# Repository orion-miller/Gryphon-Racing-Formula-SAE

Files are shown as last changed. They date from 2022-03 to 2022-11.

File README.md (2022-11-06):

# About
The chance to be a member of the Gryphon Racing Formula SAE team was the highlight of my time at the University of Guelph. The role helped me to appreciate the complexity of real-world systems, the necessity to make data driven decisions while remembering the limitations of my knowledge and methods, and the need for validation of results and continual reassessment. The race team was a way to gain practical experience across many stages of the engineering process, such as systems analysis, mechanical design, CAD, structural analysis and FEA, and manufacturing.

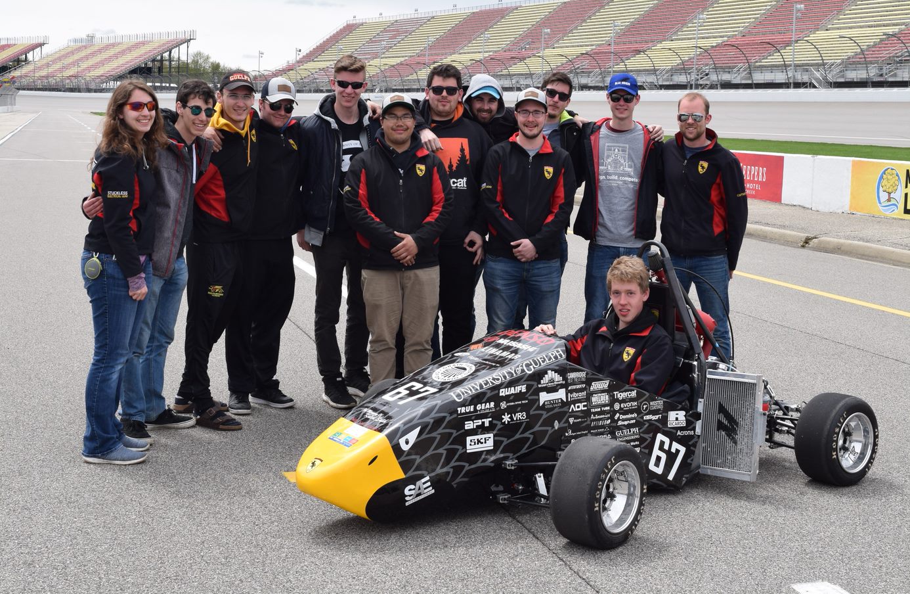
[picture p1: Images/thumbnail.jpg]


---

> ### 2018-2019: Suspension Lead
> • Managed a team of 7 people carrying out the design and manufacturing of suspension and steering components  
• Responsible for performing vehicle dynamics analysis to set systems-level design goals for an open wheeled race car   
• Designed all-new suspension and steering setups for an updated 10" wheel package  
• Manufactured numerous parts including bellcranks, suspension links, anti-roll bars, steering column, etc.  
• Received highest Suspension Design score at competition since team inception in 2002, and was one of the team's 4 competition drivers  
• Developed a MATLAB based program for visualizing tire test data and fitting Semi-Empirical Pacejka tire models, using data generated by the FSAE Tire Testing Consortium  
• Completed two group design projects for course credit, developing a carbon fibre rim design and shock dynomometer

> ### 2017-2018: Suspension Member
> • Design and manufacturing of custom steering rack and steering column assembly  
• Machining of various parts using manual mill, manual lathe, CNC mill  
• Attendance of team events for sponsorship and promotion  

> ### 2016-2017: Chassis Member
> • Helped with building of a steel space frame chassis & general fabrication for frame components   
• Design of pedal box assembly  

---
## Design & Manufacturing Work - Examples
---

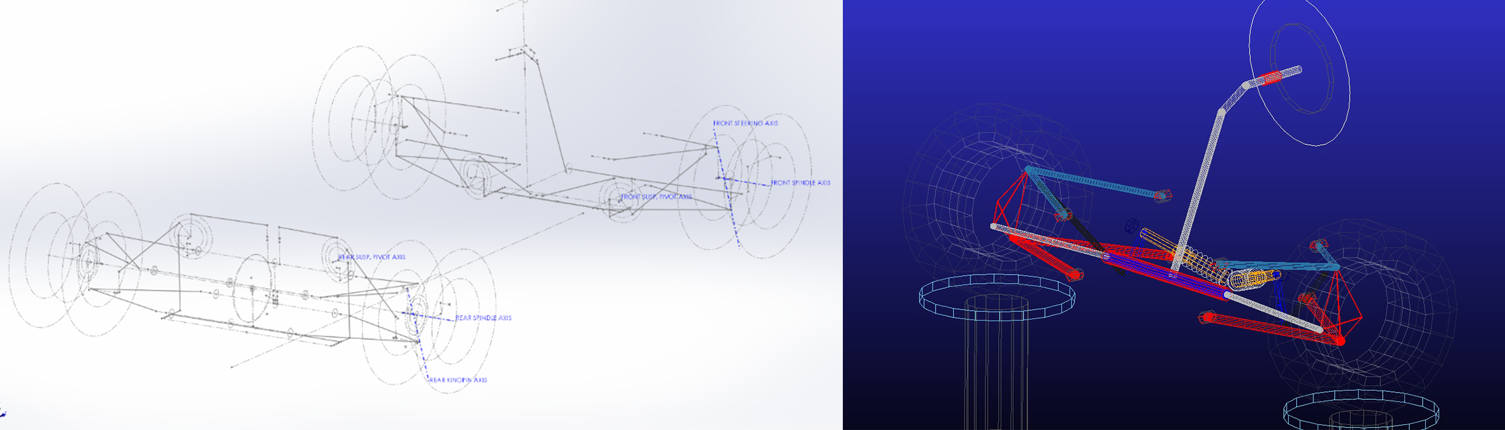
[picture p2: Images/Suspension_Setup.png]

*2019 Suspension Setup*

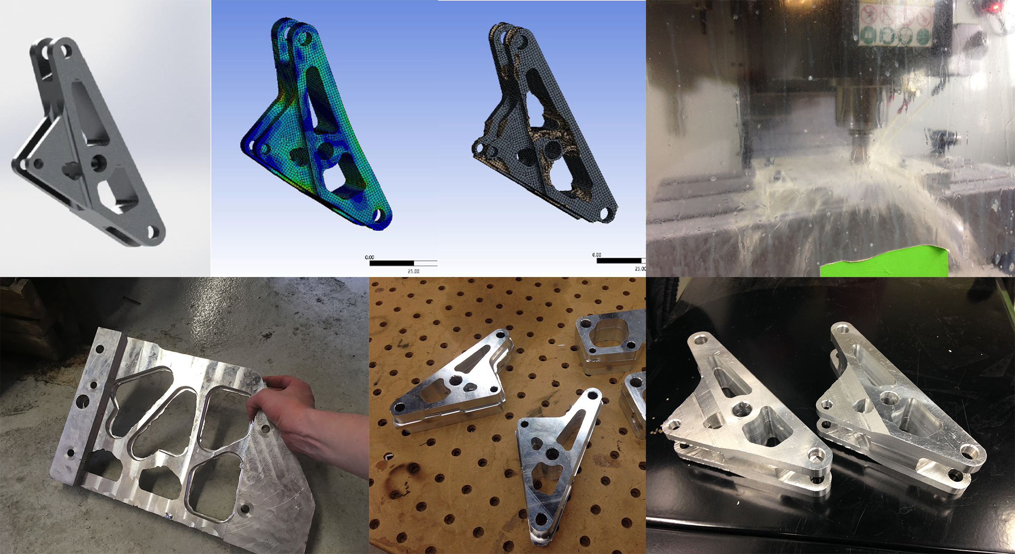
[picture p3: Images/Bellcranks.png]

*Bellcranks*

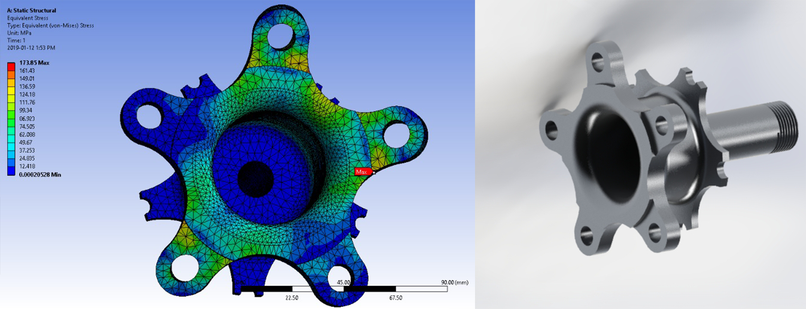
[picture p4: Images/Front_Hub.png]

*Front Hubs*

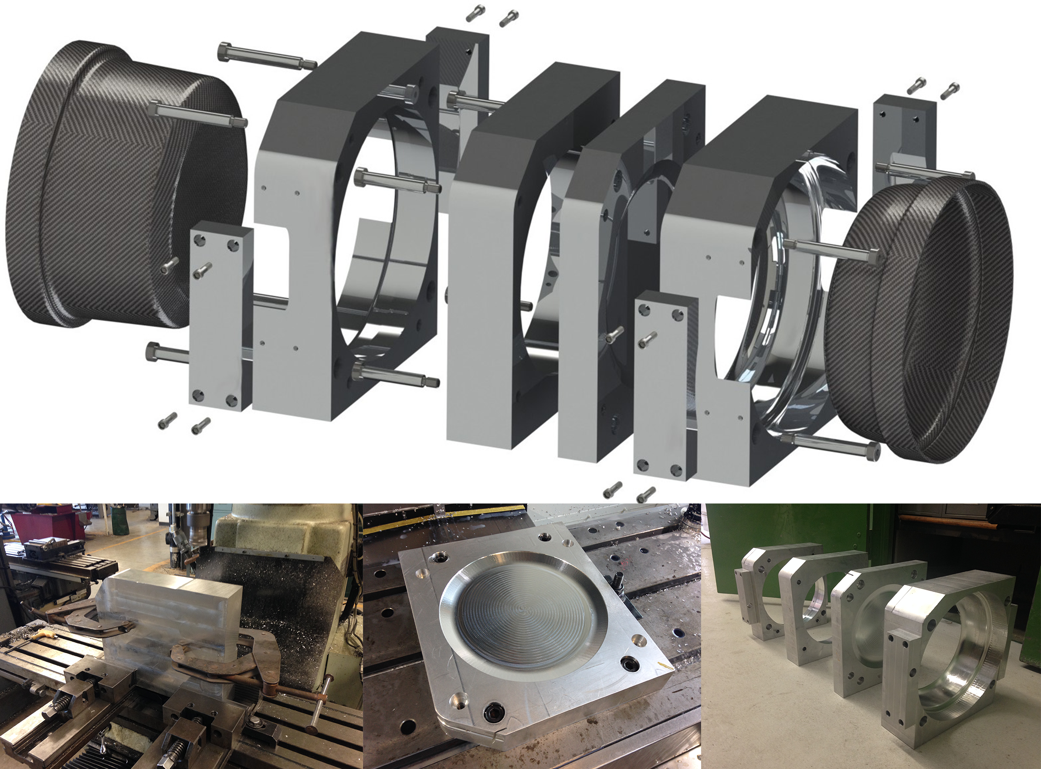
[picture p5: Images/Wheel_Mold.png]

*Carbon Fiber Rim Mold*

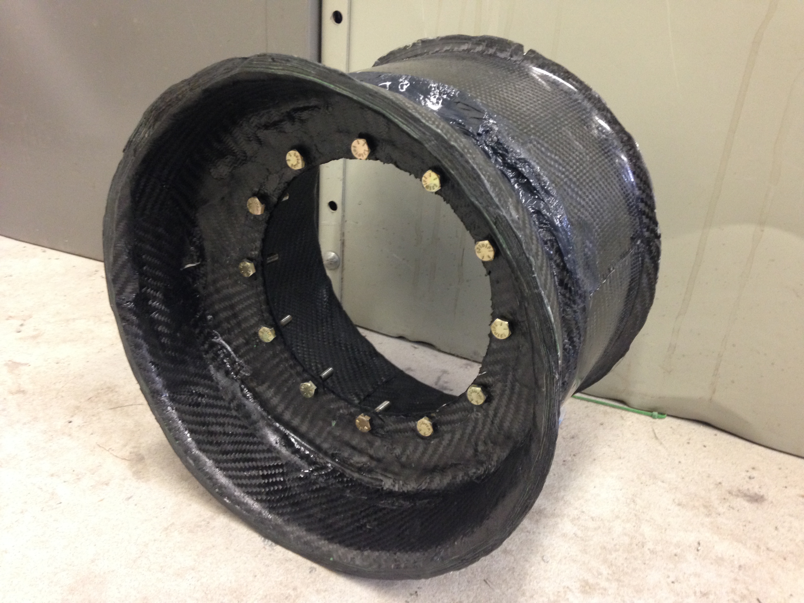
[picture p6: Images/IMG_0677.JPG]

*Carbon Fiber Rim*

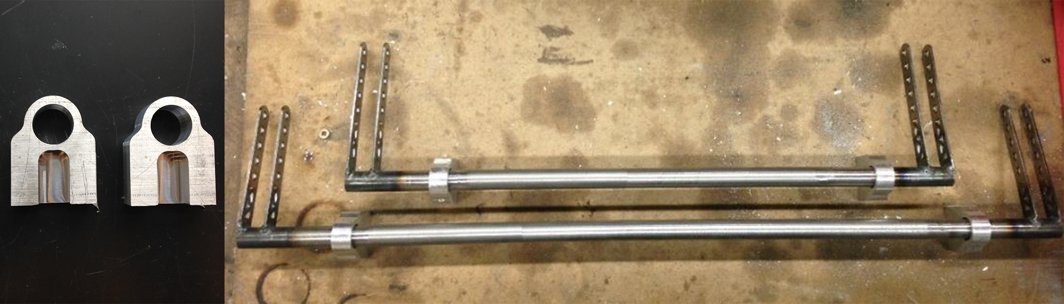
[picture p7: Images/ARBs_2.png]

*Anti-Roll bars*

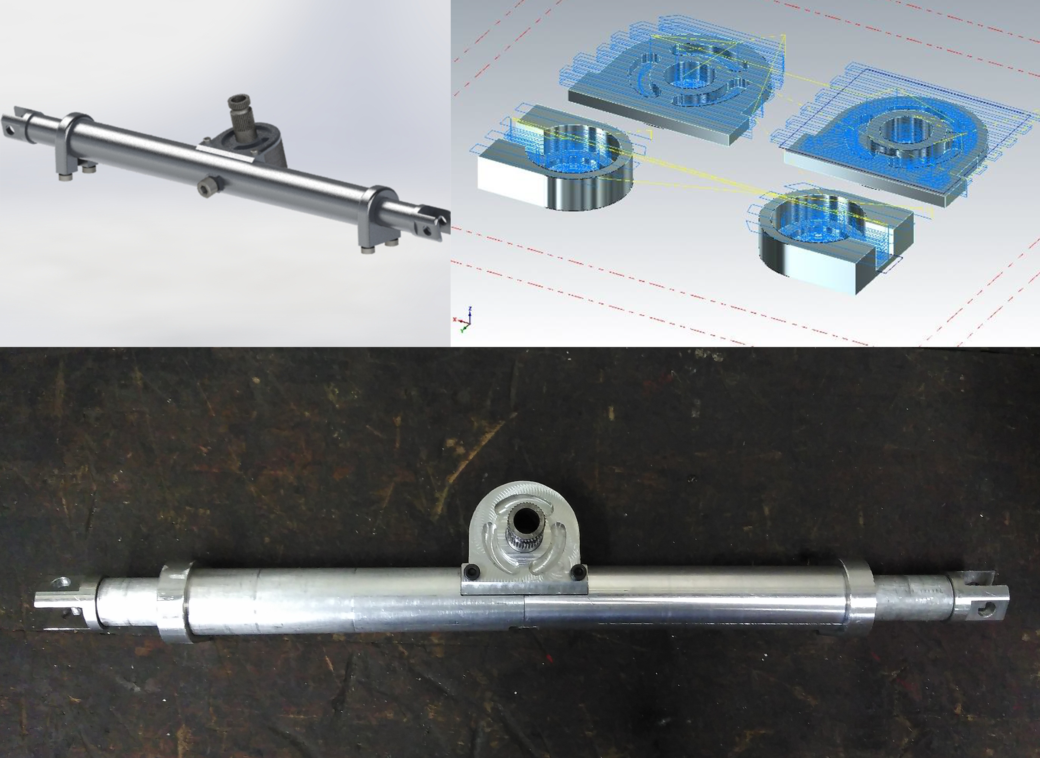
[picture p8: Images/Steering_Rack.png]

*Custom Steering Rack*

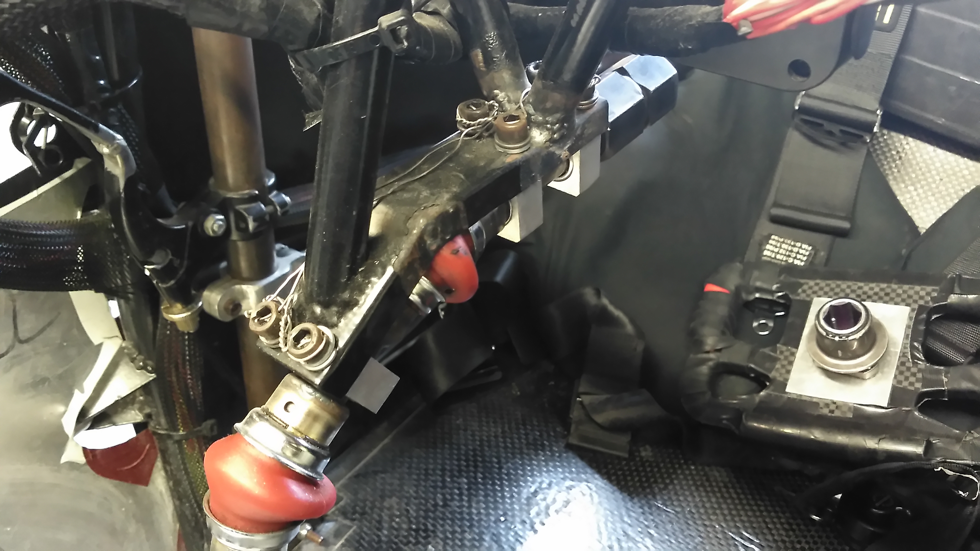
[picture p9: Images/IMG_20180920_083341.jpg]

*Steering Column*

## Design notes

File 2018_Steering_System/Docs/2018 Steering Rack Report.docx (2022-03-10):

Orion Miller 2018 Custom Steering Rack Report April 21st, 2018.

Background

In the teams most recent car (GRC-17), a Kaz Technologies steering rack is used in a bottom mount, rear steer configuration. This rack is reliable and functions well, however when scrutinizing the overall weight of the system, there appear to be opportunities for improvement.

Firstly, the location of the mounts on the rack created the need to add two more frame members through the middle of the cockpit floor. The weight of these tubes is estimated to be 441 grams (0.83 lbs). If a slightly longer rack were used, it would be possible to avoid this by mounting on to the existing outside frame members.

Secondly, a different material could be chosen for the rack gear. Using aluminum over steel would reduce weight significantly for such a large component. The density of steel is 7700 kg/m³, whereas aluminum is only 2700 kg/m³. The reason aluminum is less commonly used is because aluminum gears are prone to galling. However, the life cycle of an FSAE car is quite short, and the weight reduction benefits are large enough to justify the inconvenience of possibly having to replace the rack gear on a yearly basis.

Design Goals

Because of the lack of available steering racks that are designed to mount on the outside of the frame, are lighter than the Kaz rack, and are affordable, the development of a custom rack is the best option. The requirements for this design are as follows:

Constraints

- This rack should have a similar speed ratio (4.8 in/rev) and overall travel (3.25”) to the previous system, because the team was satisfied with its performance.
- The journal bearings should be mounted on the outside of the system to minimize the lengths of the bending moments for the longer rack gear.
- The housing of the system needs to effectively keep the grease in, and any dust or dirt out.
- The system needs to be built to withstand estimated maximum steering forces of 2000 N.
- Because reliability is critical for a steering system, all components must be designed for a factor of safety of 1.5 or greater.

Criteria

Development

Checking the geometry of the frame in CAD, the outside frame members are around 320 mm apart in the section where the system would be mounted. If brackets are attached on the immediate inside of these tubes, a distance between mounts of 300-305 mm should be suitable.

A pinion gear with a speed ratio of 4.8 in/rev from a previous year’s steering rack was selected.

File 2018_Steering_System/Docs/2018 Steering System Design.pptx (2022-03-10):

## 2018 Steering System Design

## Steering Rack

## Last Year’s Setup

- Functioned well
- Ackermann and speed ratio could be increased
- Heavy

## Design Goals/Constraints

- Rack must mount on outside of the frame
- Make lighter than previous
- Keep handling parameters the same
- We have to be able to make it
- Keep cost down

## What decisions were made?

- Aluminum rack
- Same gearing
- Carbon Fiber in Housing
- Slightly less overall travel (less rack teeth)
- Place bushings on outside
- Lash adjustment

## Steering Column

## Last Year’s Setup

- Compliance
- Heavy

## Design Goals/Constraints

- Simplify/reduce housing material
- Reduce compliance
- Look into shortening attaching frame members
- Joints must run under acceptable angles

## What decisions were made?

- Two shaft setup with double u-joint. Allows for Ackermann we want, simpler to constrain well
- Use same kind of U-joints, shafts, quick release
- Change from ball bearings to needle roller bearings
- Make replacement quick release hex from aluminum

## Weight Savings

- Steering Rack

- Steering Column

- Steering Rack: 1404g → 746g = 658g
- Support Material: 441g → 46g = 395g
TOTAL = 1448 grams = 3.19 lbs

- Steering Column: 617g → 498g = 119g
- Steering Housing: 296g → 111g = 185g
- Support Material: Save 91 grams

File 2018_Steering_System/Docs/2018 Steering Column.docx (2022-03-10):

2018 Steering Column

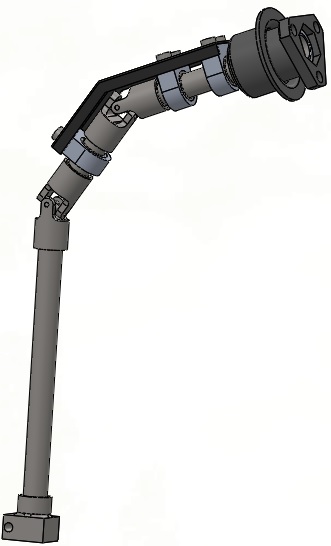
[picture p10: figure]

Specifications:

Total Weight = 1.59 lbs = 720.0 grams

Material: 1018 Steel, Aluminum

Joint Angles: 34 degrees (In Phase)

Wall Thickness = 0.035” (Minimum)

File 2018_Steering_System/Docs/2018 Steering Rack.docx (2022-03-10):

2018 Steering Rack

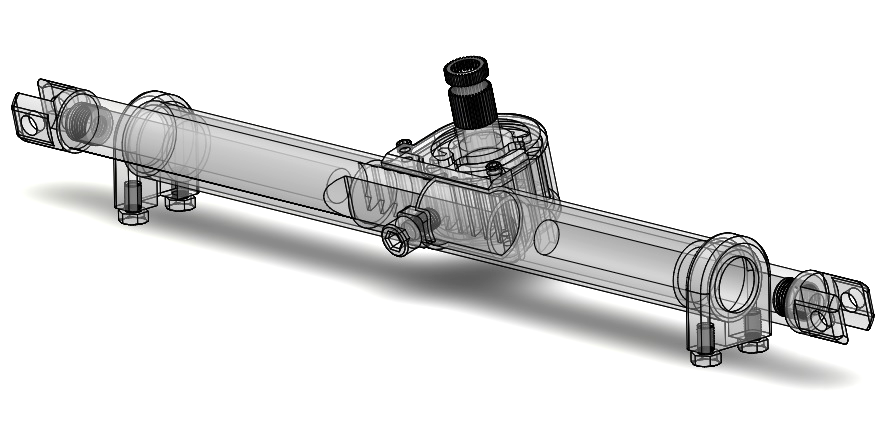
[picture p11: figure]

Specifications:

Total Weight = 1.64 lbs = 743.5 grams

Material: 6061 Aluminum, High Carbon Steel, Carbon Fiber

Length (Pickup to Pickup) = 15.96 in = 404.5 mm

Total Travel = 2.7 in = 68 mm

Speed Ratio = 4.81 in/rev

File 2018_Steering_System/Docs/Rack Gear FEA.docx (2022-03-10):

# Steering Rack FEA 04/25/2019

# Assumptions

- Resultant force of 2000N applied at a 15 degree angle
- Support reaction occurs on the face of a single tooth
- Rack surface is a frictionless slider

# Material Properties

Model Reference | Properties

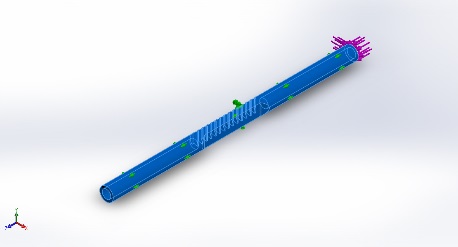
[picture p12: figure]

| Name: 6061-T6 (SS) Model type: Linear Elastic Isotropic Default failure criterion: Unknown Yield strength: 2.75e+008 N/m^2 Tensile strength: 3.1e+008 N/m^2 Elastic modulus: 6.9e+010 N/m^2 Poisson's ratio: 0.33 Mass density: 2700 kg/m^3 Shear modulus: 2.6e+010 N/m^2 Thermal expansion coefficient: 2.4e-005 /Kelvin

Mesh Details

- Mesh Type: Automatic
- Number of Cells: 13875
- Refinement: No
- Topology Criteria: NA
- Topology Percentage: NA

# Loads and Fixtures

Fixture Name | Fixture Image | Fixture Details

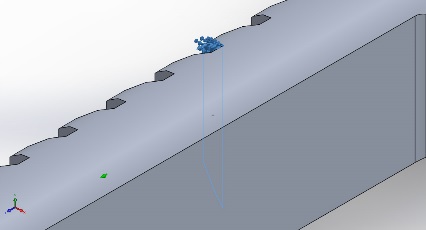
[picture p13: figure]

Fixed-5 | | Entities: 1 face(s) Type: Fixed Geometry

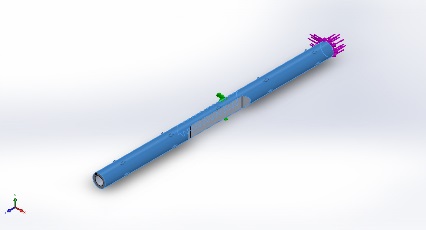
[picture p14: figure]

Roller/Slider-4 | | Entities: 1 face(s) Type: Roller/Slider

Load Name | Load Image | Load Details

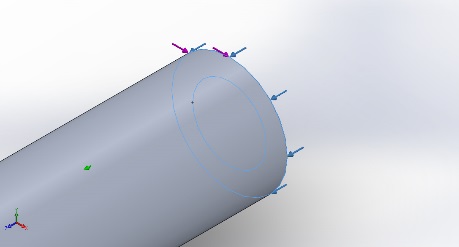
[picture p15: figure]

Force-3 | | Entities: 1 face(s) Type: Apply normal force Value: 1930 N

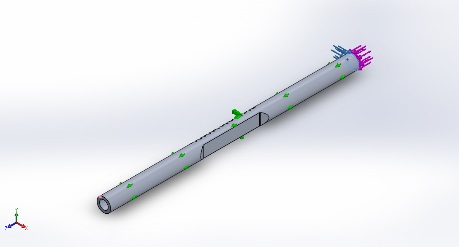
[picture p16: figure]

Force-4 | | Entities: 1 face(s) Type: Apply force Values: 520 N

# Study Results

Name | Type | Max
Stress | VON: von Mises Stress | 1.648e+007N/m^2

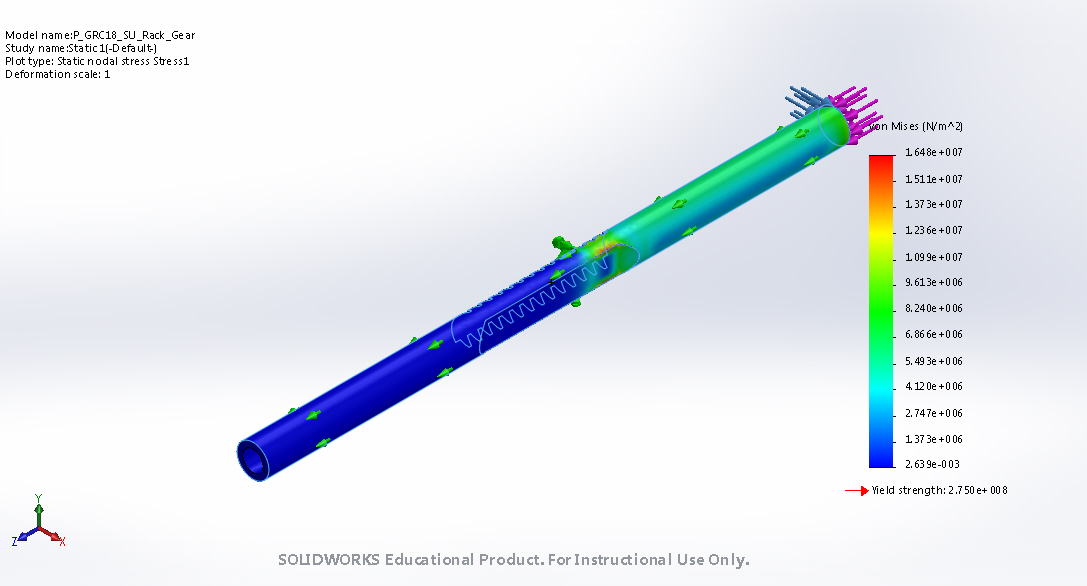
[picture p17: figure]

Name | Type | Max
Displacement | URES: Resultant Displacement | 2.464e-002mm

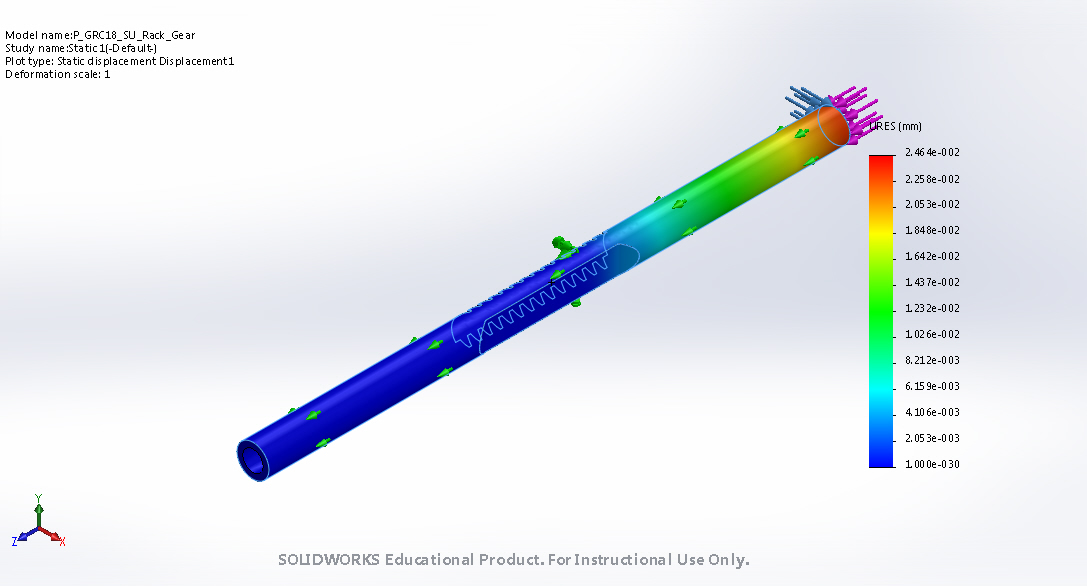
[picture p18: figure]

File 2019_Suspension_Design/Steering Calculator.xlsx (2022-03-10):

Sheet: Steering Radius
VARIABLE |  | UNITS | VARIABLE |  | UNITS
Wheelbase | 1.55 | m | CG X-Location | 0.8 | m
Rear Track | 1.196 | m | CG Y-Location | 0 | m
Front Track | 1.231 | m | Rear Inside Fx | 1000 | N
Rear Inside Slip Angle | 3.1 | deg. | Rear Inside Fy | 1200 | N
Rear Outside Slip Angle | 4.4 | deg. | Rear Inside Mz | 50 | N.m
Front Inside Slip Angle | 7.2 | deg. | Rear Outside Fx | 1500 | N
Front Outside Slip Angle | 8.8 | deg. | Rear Outside Fy | 2000 | N
Turn Radius | 4 | m | Rear Outside Mz | 50 | N.m
REQUIRED GEOMETRY |  |  | Front Inside Fx | 1000 | N
Inside Steering Angle | 24.62 | deg. | Front Inside Fy | 1400 | N
Outside Steering Angle | 22.23 | deg. | Front Inside Mz | 50 | N.m
Ackermann Angle | 2.38 | deg. | Front Outside Fx | 1300 | N
 |  |  | Front Outside Fy | 1700 | N
 |  |  | Front Outside Mz | 50 | N.m
Sources of Inaccuracy |  |  | Aerodynamic Mz | 80 | N.m
What slip angles should be used? |  |  | Yaw Moment | 8075.65 | N.m
**Trig stuff - don't worry about what these are** |  |  | **Counterclockwise Rotation is Positive**
Rear Angle | 3.75 | deg. | **CG X-Location is distance from back of car to CG**
Rear y dist to center | 4.598 | m | **Positive CG Y is towards the outside of the car**
Rear x dist | 0.3005097892 | m | M1 | 598
Front inside x dist | 1.249490211 | m | M2 | 960
front inside y dist | 3.9825 | m | M3 | 897
front outside x dist | 1.249490211 | m | M4 | 1600
front outside y dist | 5.231 | m | M5 | 615.5
front inside w/o slip | 17.41899825 | deg. | M6 | 1050
front outside w/o slip | 13.43409791 | deg. | M7 | 800.15
 |  |  | M8 | 1275

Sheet: S.S. Steering Effort
VARIABLE | OUTSIDE TIRE | INSIDE TIRE | UNITS
Mz | 100 | 80 | N.m
Pneumatic Trail | 0.03 | 0.03 | m
Mechanical Trail | 0.04 | 0.04 | m
Steering Pickup Length | 0.055 |  | m
Steer Angle (δ) | 20 | 25 | deg.
Tie-Rod Length | 0.35 |  | m
Tie-Rod Angle (θ) | 18 | 14 | deg.
Pinion Gear Pitch Radius | 0.018 |  | m
Steering Wheel Width | 0.12 |  | m
SYSTEM FORCES
Resultant Lateral Force on Tire | 1428.57 | 1142.86 | N
Force on Upright Pickup | 1818.18 | 1454.55 | N
Tie-Rod Force | 1819.29 | 1871.65 | N
Axial Force at Rack Clevis | 1730.25 | 1816.05 | N
Transverse Force at Rack Clevis | 562.19 | 452.79 | N
Axial Force Reacted By Pinion | 3546.30 |  | N
Force at Wheel | 531.95 |  | N
Sources of Inaccuracy
Where do Mz's and pneumatic trail come from?

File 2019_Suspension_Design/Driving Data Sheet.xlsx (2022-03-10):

GRYPHON RACING TEST DAY SHEET
DATE: | AIR TEMP: |  |  | WEATHER:
TIME: | ROAD TEMP: |  |  | LOCATION:
TEST PLAN:
 | FR | FL | RR | RL | NOTES
SHOCK PRELOAD |  |  |  |  | mm, measure exposed threads
CORNER WEIGHT |  |  |  |  | lbs
WEIGHT DISTRIBUTION |  |  |  |  | %
BRAKE BALANCE |  |  |  |  | %
CAMBER |  |  |  |  | colours of shims
TOE |  |  |  |  | deg
SHOCK SPRING RATE |  |  |  |  | lbs/in
SHOCK LSC |  |  |  |  | clicks from closed
SHOCK HSC |  |  |  |  | clicks from closed
SHOCK LSR |  |  |  |  | clicks from closed
SHOCK HSR |  |  |  |  | clicks from closed
ARB POSITION (1-5) |  |  |  |  | 1-5, 5 tightest
TIRE TEMP INSIDE - START |  |  |  |  | C
TIRE TEMP CENTER - START |  |  |  |  | C
TIRE TEMP OUTSIDE - START |  |  |  |  | C
TIRE PRESSURE - START |  |  |  |  | psi
TIRE TEMP INSIDE - END |  |  |  |  | C
TIRE TEMP CENTER - END |  |  |  |  | C
TIRE TEMP OUTSIDE - END |  |  |  |  | C
TIRE PRESSURE - END |  |  |  |  | psi
GAS LEVEL |  | ENGINE TUNE
GAS BATCH
OIL LEVEL |  | CV GREASE
OIL BATCH |  | FUEL FILTER
COOLANT LEVEL |  | AIR FILTER
DRIVER FEEDBACK (AS SPECIFIC AS POSSIBLE) AND CHANGE NOTES:

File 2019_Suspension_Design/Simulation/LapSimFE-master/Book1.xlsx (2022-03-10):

Classes | Notes | Functions | Notes
Motor | Should be complete except for commenting. Optimization is complete. Needs torque and efficiency data.
Battery | Not Started
Driveline | Not Started
Suspension | Not Started
CarTire | Currently defined by a simple GG curve Current state is fully documented
Brakes | Not Started
Car | Old version still available, can possibly rip a few methods out of there
Track | Completed
Track Section | Needs to add throttle/brake curve property Current state is fully documented

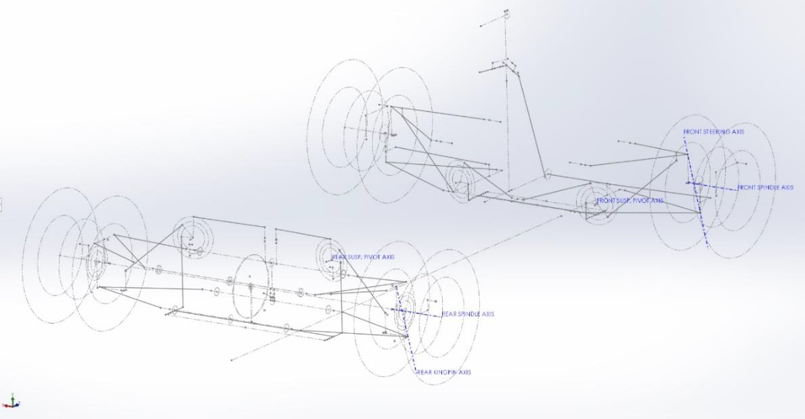
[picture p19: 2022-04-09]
Images/Design_Sketches.png

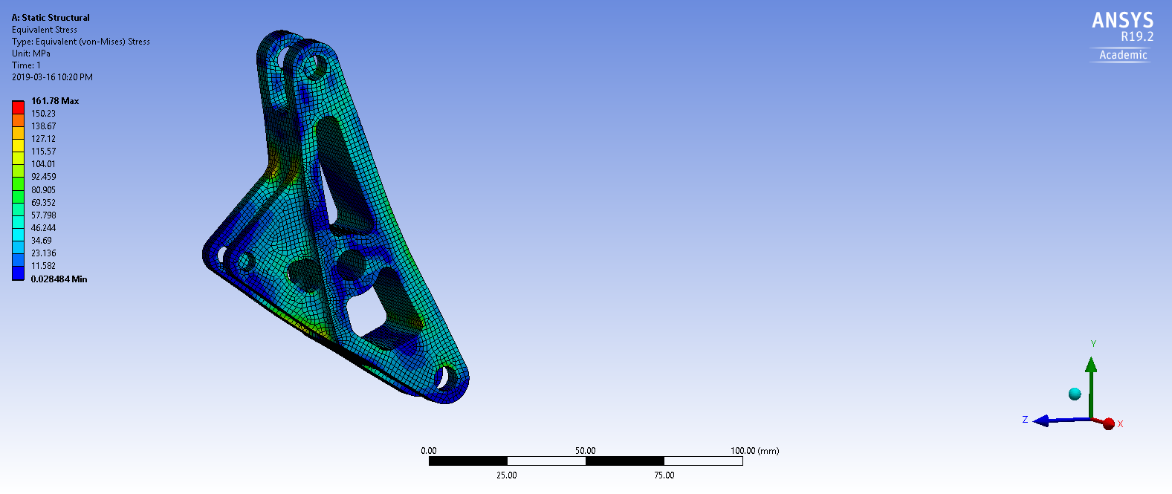
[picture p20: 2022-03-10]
2019_Suspension_Design/Screenshots & Pictures/Renders/Untitled.png

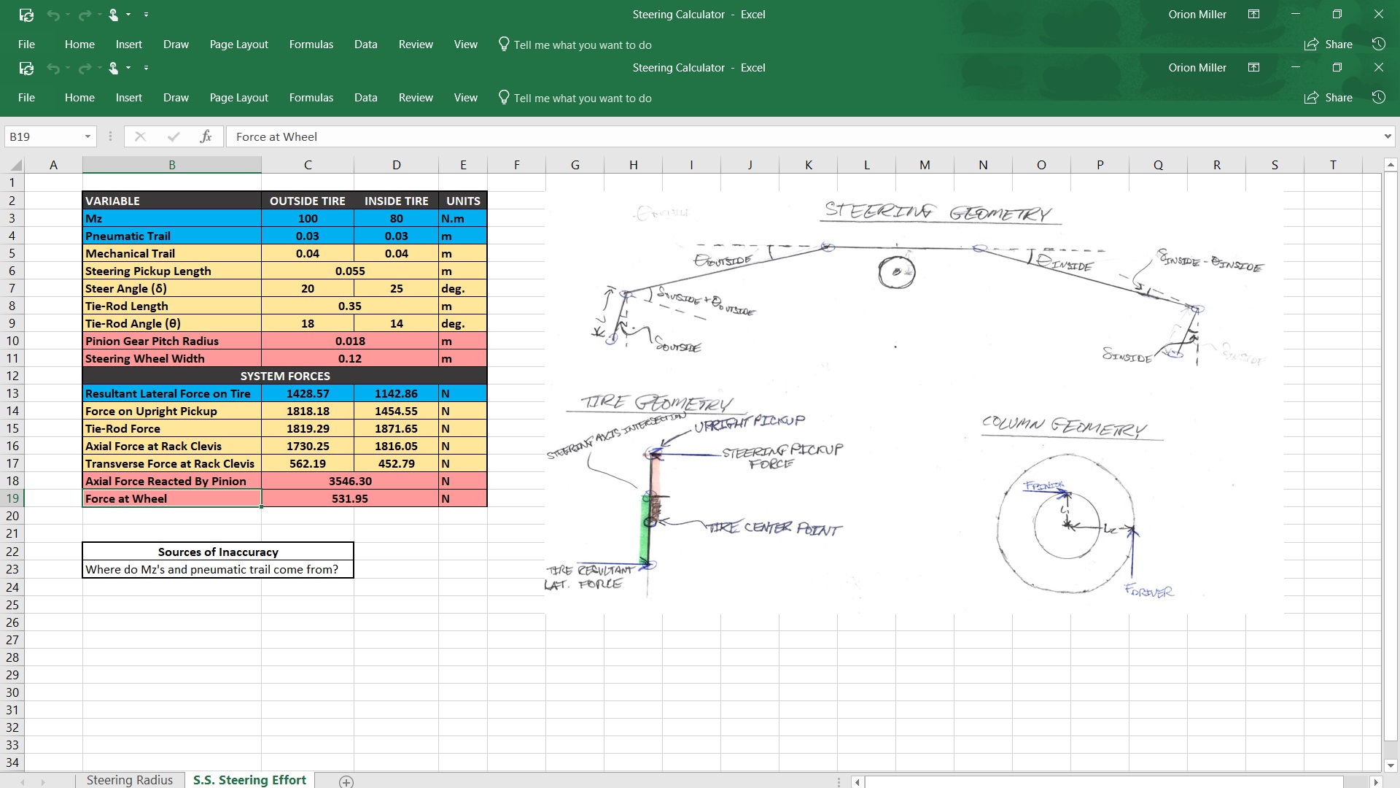
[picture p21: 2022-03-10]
2019_Suspension_Design/Screenshots & Pictures/Steer sheet 2.jpg

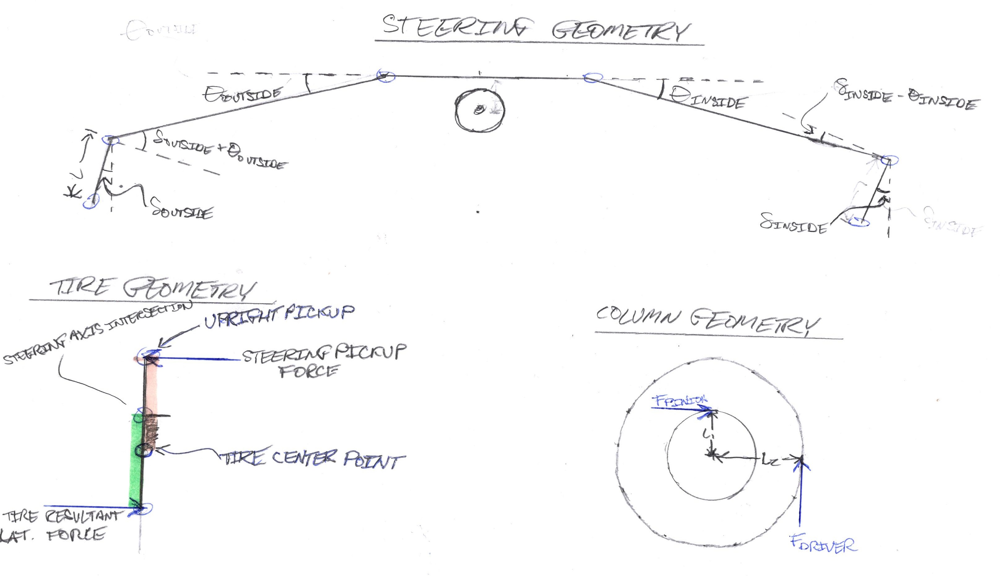
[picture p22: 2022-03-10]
2019_Suspension_Design/Screenshots & Pictures/Steer Diagram.jpg

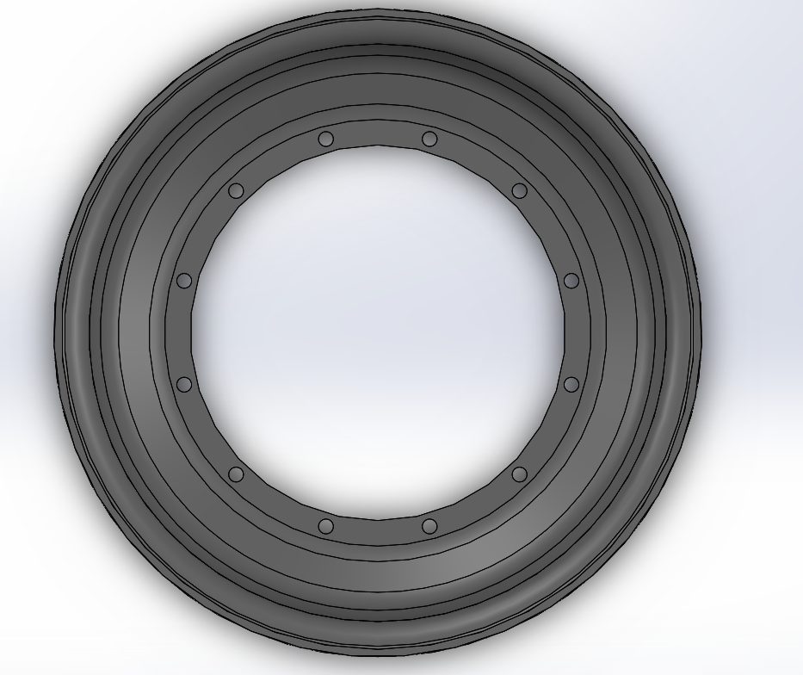
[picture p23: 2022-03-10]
2019_Suspension_Design/Screenshots & Pictures/orion24.png

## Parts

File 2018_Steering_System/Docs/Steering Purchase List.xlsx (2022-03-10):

Part | # | Cost | Supplier | Model # | Link
Quick Release | 1 | 40USD +? | Speedway Motors | 91032892 | https://www.speedwaymotors.com/Aluminum-Rim-Style-Quick-Release-Hub-3-4-Inch,32478.html
Carbon Fibre Tubes | 2 | 156USD +? | Rock West Composites | 45530 | https://www.rockwestcomposites.com/45530
Rack Journal Bearings | 2 | 5.80USD +? | Bronze Bushings | 101438 | http://www.bronzebushings.com/sae-841/aa-1041-2-oil-impregnated-bronze-sleeve-13-16-id-x-1-od-x-7-8-oal.html
Column Needle Bearings | 3 | 26.40USD +? | Bearings Canada | BA107ZOH | https://www.bearingscanada.com/BA107ZOH-Needle-Bearing-5-8-x13-16-x7-16-inch-p/ba107zoh.htm
Hardware?

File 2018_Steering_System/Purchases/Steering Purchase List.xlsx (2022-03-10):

Part | # | Cost | Shipping | Supplier | Model # | Link
Quick Release | 1 | 30 USD | 12.03 USD | Speedway Motors | 91032892 | https://www.speedwaymotors.com/Aluminum-Rim-Style-Quick-Release-Hub-3-4-Inch,32478.html
Column Needle Bearings | 3 | 21.60 CAD | 13.09 CAD | Bearings Canada | BA107ZOH | https://www.bearingscanada.com/BA107ZOH-Needle-Bearing-5-8-x13-16-x7-16-inch-p/ba107zoh.htm
Rack Journal Bearings | 2 | 11.6 USD |  | Bronze Bushings | 101438 | http://www.bronzebushings.com/sae-841/aa-1041-2-oil-impregnated-bronze-sleeve-13-16-id-x-1-od-x-7-8-oal.html
5/8 Tube 0.035, 2ft | 1 | 14.68 USD | 52.43 USD | Online Metals
3/4 Tube, 1 ft | 1 | 6.93 USD |  | Online Metals
13/16 Aluminum Bar, 2ft | 1 | 12.6 USD |  | Online Metals | 18035 | https://www.onlinemetals.com/merchant.cfm?pid=18035&step=4&showunits=inches&id=1277&top_cat=60
Aluminum Tubing, 2 ft | 1 | 24.4 USD |  | Online Metals | 6997 | http://www.onlinemetals.com/merchant.cfm?pid=6997&step=4&showunits=inches&id=71&top_cat=0
Hardware?
 | Total = | #VALUE!

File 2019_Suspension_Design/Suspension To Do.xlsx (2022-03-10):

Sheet: Design
Job | Done By | Finish By
Finalize rear suspension, fix clearances | Orion | Jan 6th
ARB Geometry + Mount Locations | Orion | Jan 6th
Finalize Steering Geometry | Orion | Jan 6th
Update Design Spreadsheet | Orion | Jan 6th
Update Adams Model | Orion | Jan 6th
A-Arms Final CAD | Will | Jan 6th
Shock Cover Design | Orion | Jan 6th
Steering System Final CAD | Orion | Jan 6th
Front ARB Final CAD | Orion | Jan 6th
Rear ARB Final CAD | Orion | Jan 6th
Front Bellcrank Initial CAD | Orion | Jan 6th
Front Bellcrank FEA | Orion | Jan 6th
Front Bellcrank Final CAD | Orion | Jan 6th
Rear Bellcrank Initial CAD | Will | Jan 6th
Rear Bellcrank FEA | Will | Jan 6th
Rear Bellcrank Final CAD | Will | Jan 6th
Front Upright Initial CAD | Ryan | Jan 6th
Front Upright FEA | Ryan | Jan 6th
Front Upright Final CAD | Ryan | Jan 6th
Rear Hub Initial CAD | Matt | Jan 6th
Rear Hub FEA | Matt | Jan 6th
Rear Hub Final CAD | Matt | Jan 6th
Front Hub Initial CAD | JP | Jan 6th
Front Hub FEA | JP | Jan 6th
Front Hub Final CAD | JP | Jan 6th
Wheel Assembly/Center CAD | Orion | Jan 6th
A-Arm Mount Block CAD | Orion | Jan 6th

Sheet: Parts - Ours
Part | Quantity | Job | Done With | Material Needed | Done By | Finished By
Uprights Rear | 2 | Write CAM | CNC | 4.5" Blocks
 |  | Pre-Machine
 |  | Run CAM
 |  | Post-Machine
ARB Mounts | 4 | Write CAM | CNC | 1/2" Plate
 |  | Run CAM
 |  | Post-Machine
Steering Column Mounts | 3 | Write CAM | CNC | 1/2" Plate
 |  | Run CAM
 |  | Post-Machine
A-Arm Jig | 1 |  | Mill | 4.5" Block
Steering Column Tubes | 1 |  | Lathe | 5/8,3/4" Tube 1020 |  | Jan 4th.
U-Joints Trim |  |  | Mill | No
Steering Rack Spacers | 2 |  | Lathe | No |  | Jan 4th.
ARB's | 2 |  | Lathe | 5/8" Tube 1020 |  | Jan 4th.
A-Arm Notch + Weld | 8 |  | Manual Mill | 5/8 Tube 1020
Rod End Cone Spacers | 24 |  | Lathe | Barstock AL 1/2"
Shock Cover Mold | 1 | Write CAM | CNC | Machinable Foam
 |  | Run CAM
Uprights Rear | 2 | Write CAM | CNC | 4.5" Blocks
 |  | Pre-Machine
 |  | Run CAM
 |  | Post-Machine

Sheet: Parts - Sponsors
Part | Quantity | Done With | Material Needed | Done By | Finished By
Uprights Rear | 2 | CNC | 4.5" Blocks | APT
Hubs Rear | 2 | CNC | Yes | APT
Hubs Front | 2 | CNC | Yes | APT
Bellcranks Rear | 2 | CNC
Bellcranks Front | 2 | CNC
Frame Mount Blocks | 16 | CNC |  | Musashi?
Upright Mount Blocks | 2 | CNC |  | Musashi?
ARB Tabs | 8 | Laser Cut | Sheet Steel ___ | NPL
Camber Shims 1/8" | 14 | Laser Cut | Sheet Steel 1/8" | NPL
Camber Shims 1/16" | 6 | Laser Cut | Sheet Steel 1/16" | NPL
A-Arm Gussets/Plates | 8 | Laser Cut | Sheet Steel ___ | NPL
A-Arm Bearing Cups | 24 | Lathe | Barstock Steel 1"
Hub Washers | 2 | Lathe
Susp. Link Ends | 12 |  | Lathe | Barstock Steel 5/8"

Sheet: Parts - Ordered
Part | Quantity | Supplier | Ordered Date
~~Springs - Hyperco~~ | ~~12~~ | ~~Essex Parts~~
~~U-Joints~~ | ~~20~~ | ~~Summit Racing~~
~~Studs~~ | ~~20~~ | ~~Summit Racing~~
~~Lugs~~ | ~~20~~ | ~~Summit Racing~~
~~ARB Bushings~~ | ~~12~~ | ~~Igus Bearings~~
5/8 Tubing |  | Metal Supermarkets
Upright Ball Bearings | 8 | SKF
Spherical Bearings | 24 | SKF
Fasteners |  | Fastenal
Springs Pins | 5 | Fastenal

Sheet: Tuning
Job | Done By | Finish By

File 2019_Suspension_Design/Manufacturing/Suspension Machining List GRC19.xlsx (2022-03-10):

Part | Quantity | Done With | Material Needed | Done By | Finished By
Uprights Rear | 2 | CNC | 4.5" Blocks | Us
Uprights Front | 2 | CNC | 4.5" Blocks | Sponsor (Preferably)
Hubs Rear | 2 | CNC | No | Sponsor (Must)
Hubs Front | 2 | CNC | No | Sponsor (Must)
Bellcranks Rear | 2 | CNC |  | Sponsor (Preferably)
Bellcranks Front | 2 | CNC |  | Sponsor (Preferably)
Frame Mount Blocks | 16 | CNC |  | Sponsor (Preferably)
Upright Mount Blocks | 2 | CNC |  | Sponsor (Preferably)
ARB Mounts | 4 | CNC | 1/2" Plate | Us
Steering Column Mounts | 3 | CNC |  | Us
A-Arm Jig | 1 | CNC | 4.5" Block | Us
CNC Material Prep. | x | Manual Mill | 4.5" Blocks | Us
Steering Column | 1 | Lathe | 5/8,3/4" Tube 1020 | Us | Jan 4th.
Steering Rack Spacers | 2 | Lathe | No | Us | Jan 4th.
ARB's | 2 | Lathe | 5/8" Tube 1020 | Us | Jan 4th.
A-Arm Notch + Weld | 8 | Manual Mill | 5/8 Tube 1020 | Us
Susp. Link Ends | 12 | Lathe | Barstock Steel 5/8" | Us
Rod End Cone Spacers | 24 | Lathe | Barstock AL 1/2" | Us
Front Hub Nuts | 2 | Mill/Lathe |  | Sponsor (Must)
ARB Tabs | 8 | Laser Cut | Sheet Steel ___ | Sponsor (Preferably)
Camber Shims 1/8" | 14 | Laser Cut | Sheet Steel 1/8" | Sponsor (Preferably)
Camber Shims 1/16" | 6 | Laser Cut | Sheet Steel 1/16" | Sponsor (Preferably)
A-Arm Gussets/Plates | 8 | Laser Cut | Sheet Steel ___ | Sponsor (Preferably)
A-Arm Bearing Cups | 24 | Lathe | Barstock Steel 1" | Sponsor (Preferably)
Shock Cover Mold | 1 | CNC | Machinable Foam | Us

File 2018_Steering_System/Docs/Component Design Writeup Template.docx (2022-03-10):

Component: Steering Rack

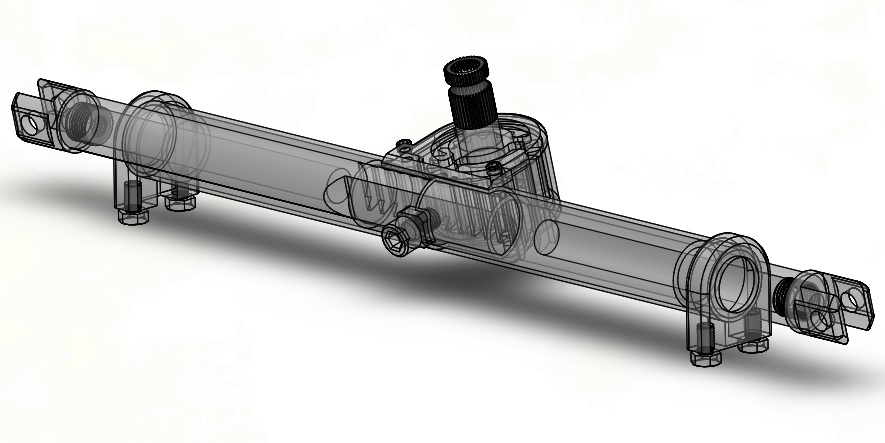
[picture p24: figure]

Problem Identification

1. What were the problems/disadvantages with previous part?
2. Which of these problems are the most important and why?

Design Goals

1. What are your strategies to solve the problems?
2. Could they produce downsides in other areas?
3. What is the “most beneficial” compromise?

Design

1. What was done in terms of the goals?
2. Any other information relevant to the design (stats, etc.)
3. Any validation?

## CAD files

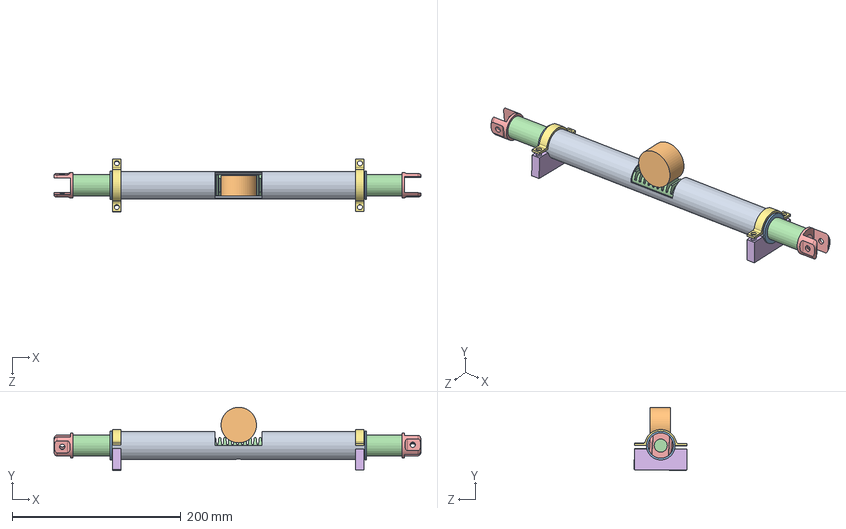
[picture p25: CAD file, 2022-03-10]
2018_Steering_System/CAD/2018 Stiletto Rack/Assem1.SLDASM
435.0 x 75.1 x 62.8 mm
Rack_Housing
Pinion Gear
Bushings x 2
Rack
Clevis x 2
Split Collar Bottom x 2
Split Collar Top x 2

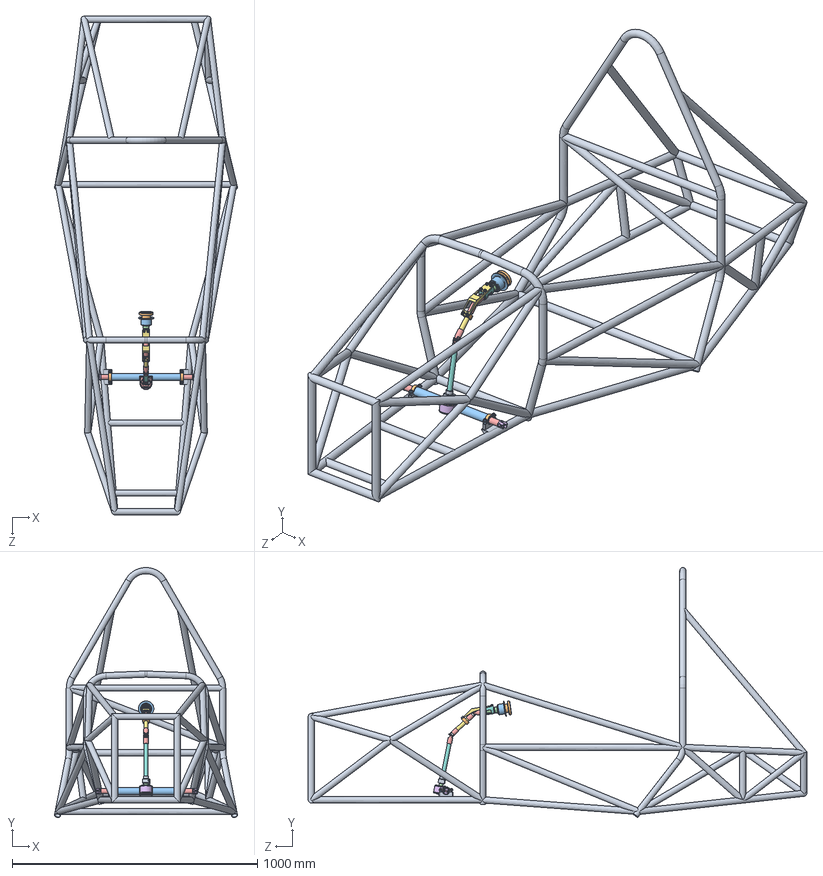
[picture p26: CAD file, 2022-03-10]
2018_Steering_System/CAD/A_GRC18_SU_STEERING_SYSTEM_REV2.SLDASM
746.9 x 1019.3 x 2033.1 mm
Frame 3.0 For Steering
Housing Main Part
CF Tubes x 2
Housing Bottom PLate
Housing Top PLate
Housing Cover
M4 Bolt x 4
Bearing x 2
Mount Bottom x 2
Mount Top x 2
Hex Bolt M6xL50mm x 4
Gear
13-16 Rack Gear
Clevis x 2
Steering Box
Bearing Housing 2
Bearing 2 x 3
Bearing Housing 3
Hex Bolt M6xL8.5mm x 6
Shaft 1
U-joint borg spec x 4
U Joint pin x 2
Shaft 2
Shaft 3
Shaft Coupler
quick release inner body
quick release outer body
quick release hex

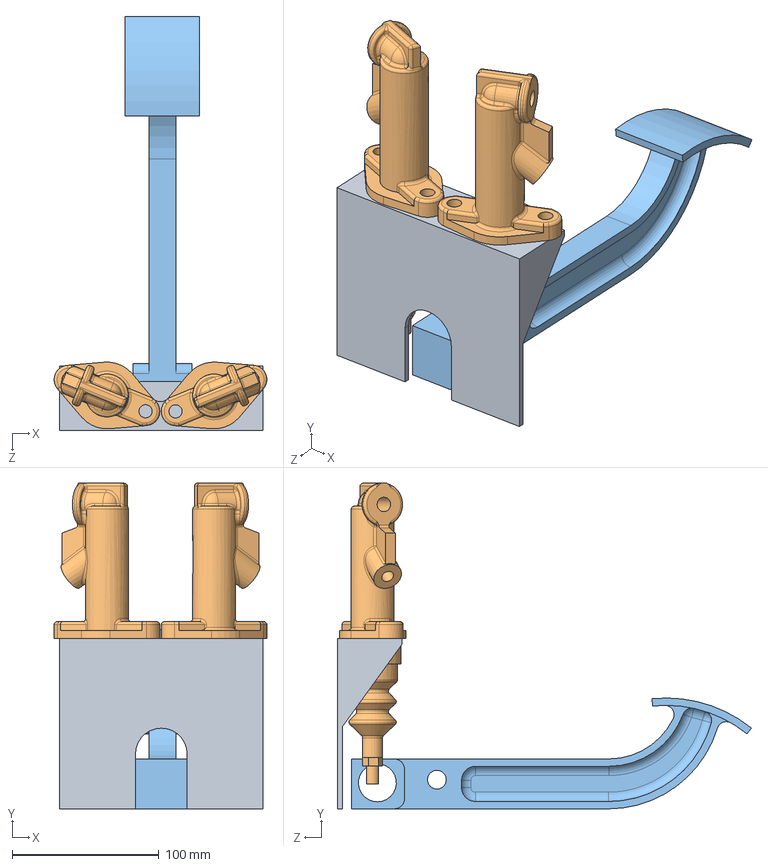
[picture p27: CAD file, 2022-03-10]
2017_Brake_Box/Brake Box Setup.SLDASM
144.9 x 221.8 x 281.9 mm
Rough Plate Brake Box
rd-mastercylinder x 2
Brake_Pedal_New

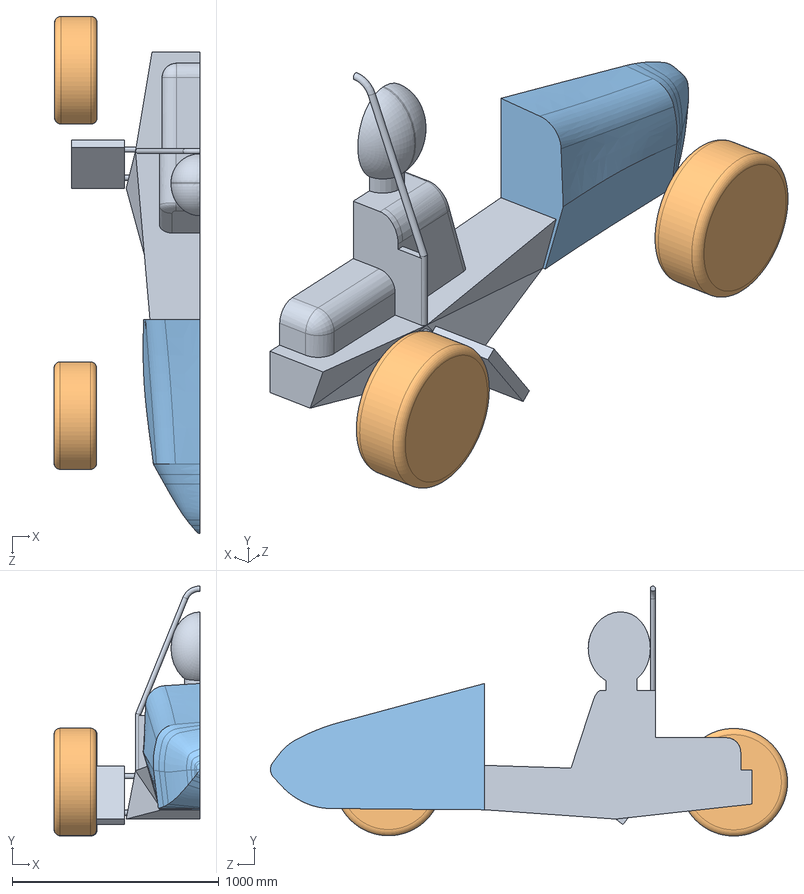
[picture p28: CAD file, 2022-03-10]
2018_Aero/CFD CAD/A_GRC18_BD_CFD_HALF_CAR_ASSEMBLY_Rev1.SLDASM
705.2 x 1208.1 x 2499.0 mm
P_GRC18_BD_CFD_HALFBODY_Rev1
P_GRC18_BD_CFD_RIMS_Rev1 x 2
P_GRC18_BD_CFD_NOSECONE_Rev1

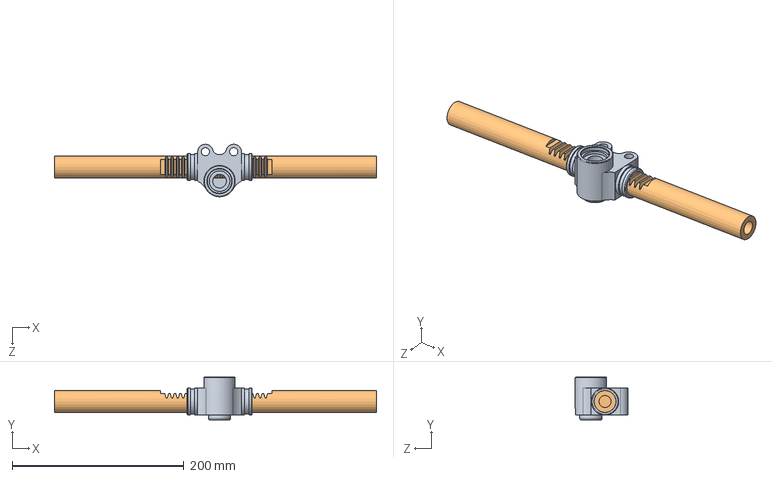
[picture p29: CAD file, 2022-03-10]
2018_Steering_System/CAD/2018 Stiletto Rack/Stiletto Rack/A_GRC18_SU_STEERING_RACK.SLDASM
375.0 x 50.0 x 61.2 mm
P_SU_GRC18_PINION_HOUSING
P_SU_GRC18_RACK_GEAR

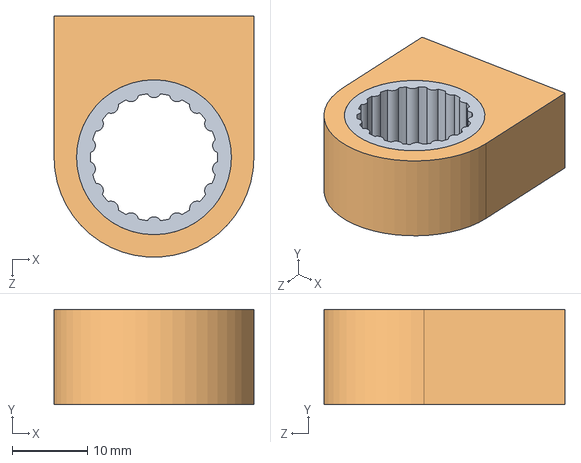
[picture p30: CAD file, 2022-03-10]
2018_Steering_System/CAD/Rev3/A_GRC18_SU_Lower_Column_Housing.SLDASM
26.6 x 12.7 x 32.1 mm
P_GRC18_SU_BA107_Bearing
P_GRC18_SU_Pillow_Block

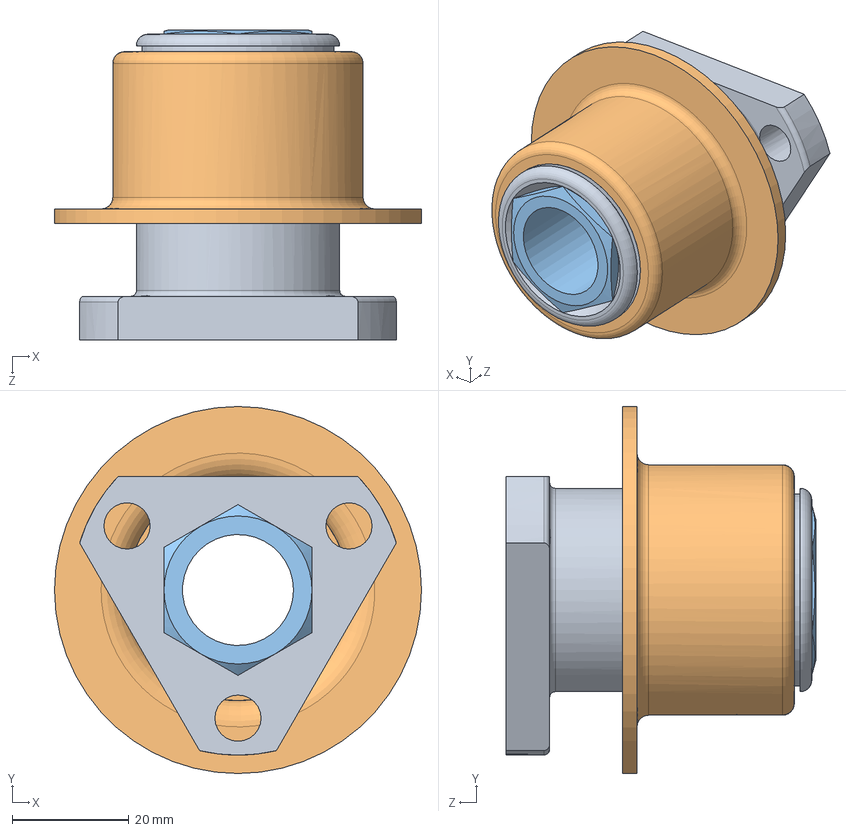
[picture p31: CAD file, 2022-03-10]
2019_Steering_System/A_GRC18_SU_Quick_Release.SLDASM
63.0 x 63.0 x 53.2 mm
P_GRC18_SU_Q.R_Inner
P_GRC18_SU_Q.R_Outer
P_GRC18_SU_Q.R_Hex

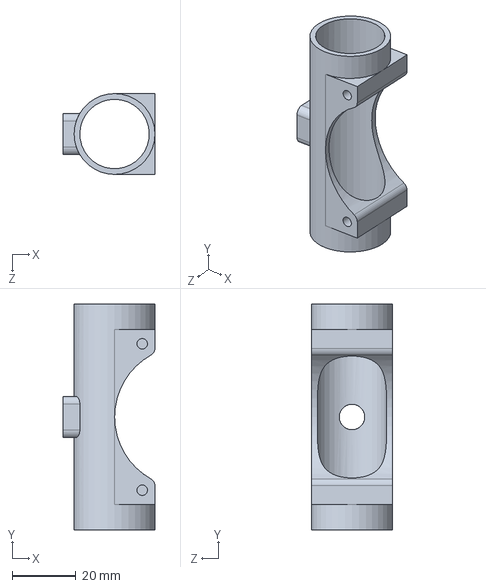
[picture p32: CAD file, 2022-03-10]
2018_Steering_System/Manufacturing/SLDPRT/CAM_GRC18_Housing_Main.SLDPRT
28.9 x 71.0 x 25.4 mm

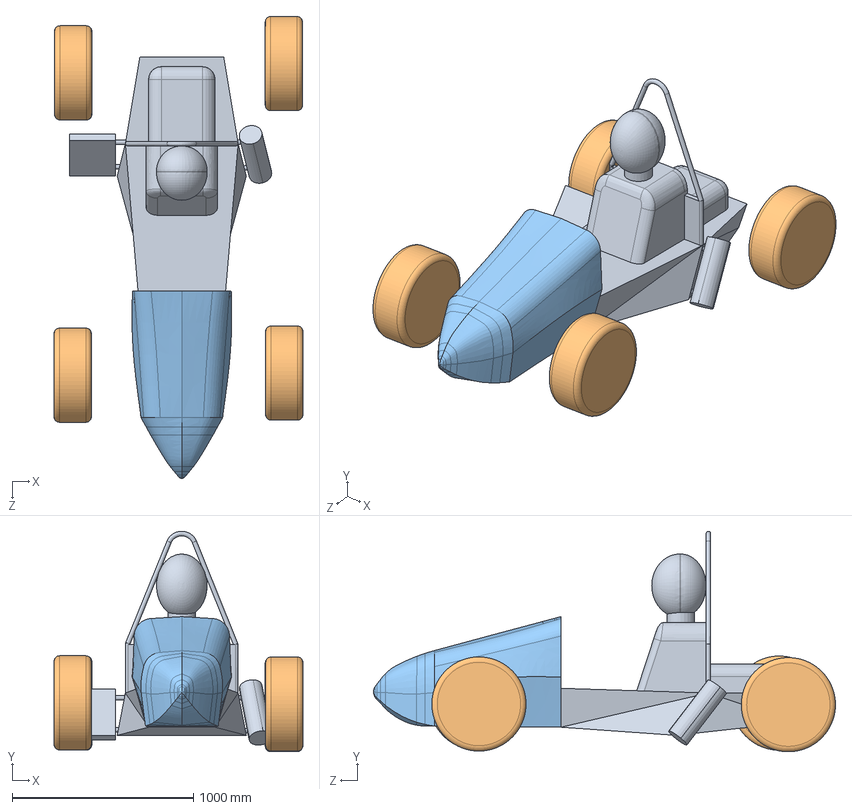
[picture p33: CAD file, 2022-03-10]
2018_Aero/CFD CAD/A_GRC18_BD_CFD_FULL_CAR_ASSEMBLY_Rev1.SLDASM
1373.6 x 1216.7 x 2549.9 mm
Rims x 4
Nosecone - Solid

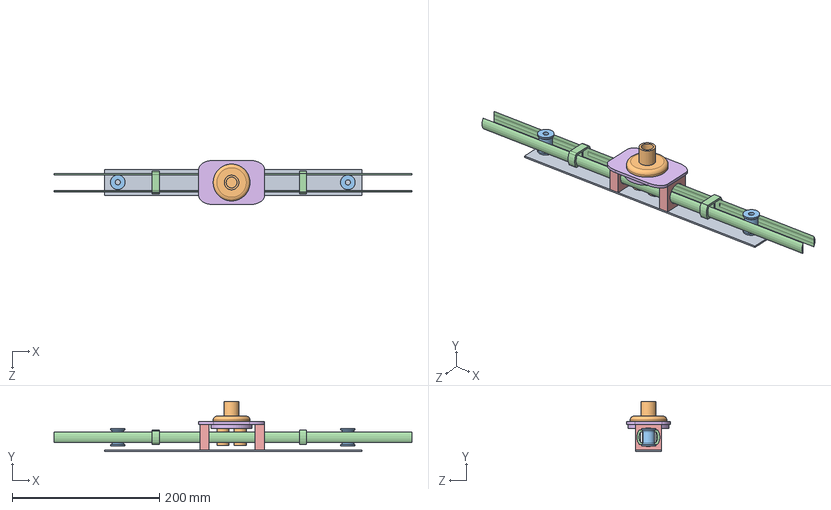
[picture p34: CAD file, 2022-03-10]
2018_Steering_System/CAD/Cable Steering/CABLE_STEERING_ASSEMBLY.SLDASM
486.0 x 68.0 x 60.0 mm
CABLE_STEERING_BASE
CABLE_STEERING_GEARS
CABLE_STEERING_PULLEYS x 2
CABLE_RACK
LINEAR_BEARING x 2
BRACKET

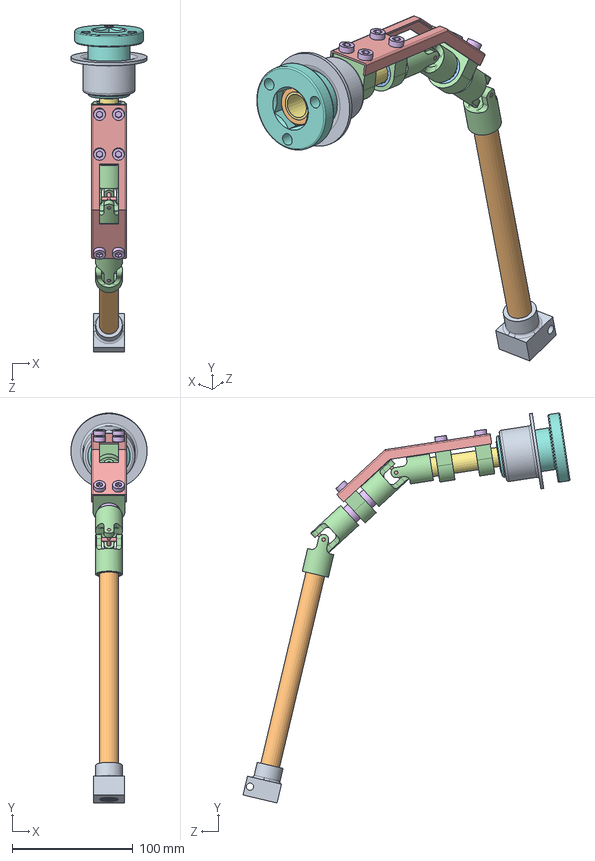
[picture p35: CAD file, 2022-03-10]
2018_Steering_System/CAD/Rev3/A_GRC18_SU_STEERING COLUMN_REV4.SLDASM
63.0 x 322.5 x 270.3 mm
P_GRC18_SU_Shaft_Coupler
P_GRC18_SU_Lower_Column
P_GRC18_SU_Lower_Column2 x 3
P_GRC18_SU_Ujoint_Shortened x 4
P_GRC18_SU_Ujoint_Pin x 2
P_GRC18_SU_Middle_Column
P_GRC18_SU_Upper_Column
P_GRC18_SU_Q.R_Inner
P_GRC18_SU_Q.R_Outer
P_GRC18_SU_Q.R_Hex
Bearing 2 x 3
P_GRC18_SU_Pillow_Block x 3
P_GRC18_SU_Column_Housing
P_GRC18_SU_M6x1.25x8.5 x 6

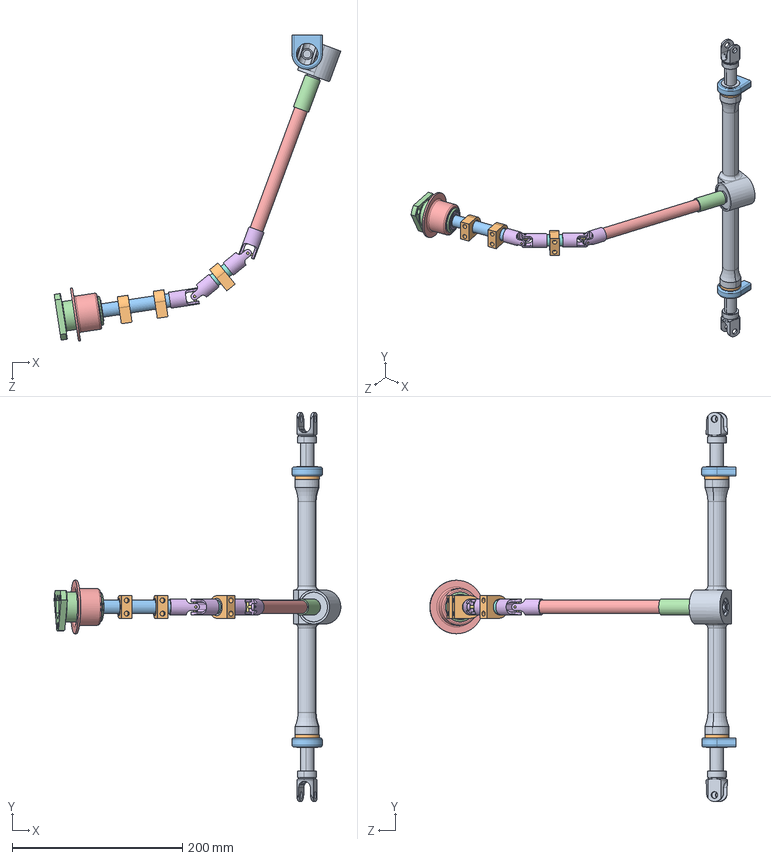
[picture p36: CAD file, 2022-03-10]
2019_Steering_System/A-STEERING ASSEMBLY.SLDASM
337.0 x 457.2 x 360.2 mm
13T-17.4 NARRco Rack V2
Mount Spacer x 2
P_GRC18_SU_Mount x 2
Shaft Coupler
P_GRC18_SU_Lower_Column
U-joint borg spec x 4
P_GRC18_SU_Ujoint_Pin x 2
P_GRC18_SU_Middle_Column
P_GRC18_SU_BA107_Bearing x 3
P_GRC18_SU_Pillow_Block x 3
P_GRC18_SU_Upper_Column
P_GRC18_SU_Q.R_Inner
P_GRC18_SU_Q.R_Outer
P_GRC18_SU_Q.R_Hex

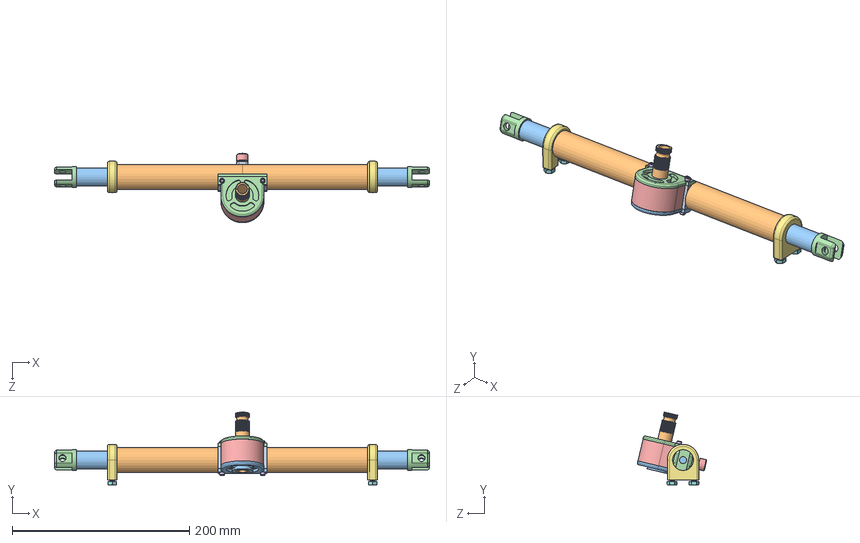
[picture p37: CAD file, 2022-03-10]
2018_Steering_System/CAD/Rev3/A_GRC18_SU_STEERING_RACK_REV6.SLDASM
423.5 x 82.4 x 78.5 mm
P_GRC18_SU_Housing_Main
P_GRC18_SU_Housing_Tubes x 2
P_GRC18_SU_Housing_Bottom_Plate
P_GRC18_SU_Housing_Top_Plate
P_GRC18_SU_Housing_Cover
P_GRC18_SU_M4x_x8 x 4
P_GRC18_SU_Mount x 2
P_GRC18_SU_M6x1.25x10 x 4
P_GRC18_SU_Journal_Bearing x 2
P_GRC18_SU_Pinion_Gear
P_GRC18_SU_Rack_Gear
P_GRC18_SU_Clevis x 2
P_GRC18_SU_M8x1.25x16

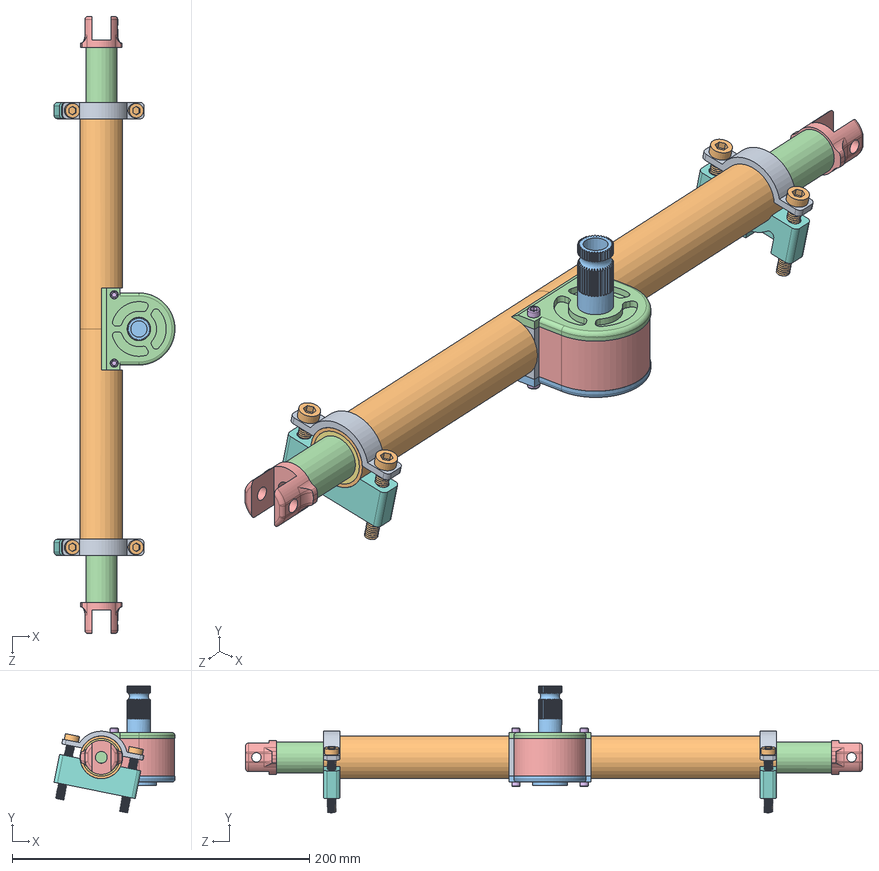
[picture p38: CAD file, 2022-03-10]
2018_Steering_System/CAD/2018 Rack/A_GRC18_SU_STEERING_RACK_REV4.SLDASM
81.5 x 85.2 x 415.5 mm
Housing Main Part
CF Tubes x 2
Housing Bottom PLate
Housing Top PLate
Housing Cover
M4 Bolt x 4
Bearing x 2
Mount Bottom x 2
Mount Top x 2
Hex Bolt M6xL50mm x 4
Gear
13-16 Rack Gear
Clevis x 2

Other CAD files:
2019_Suspension_Design/Suspension Design Sketches R8.5.SLDASM
2019_Steering_System/A_GRC18_SU_Column_Housing.SLDASM
2018_Steering_System/CAD/2018 Rack/Housing Main Part.SLDPRT
2018_Steering_System/CAD/Rev3/A_GRC18_SU_STEERING_SYSTEM_REV3.SLDASM
2017_Brake_Box/Brake_Pedal_New.SLDPRT
2017_Brake_Box/Rough Brake Box.SLDPRT
2017_Brake_Box/rd-mastercylinder.SLDPRT
2018_Aero/CFD CAD/2018 CFD Body.SLDPRT
2018_Aero/CFD CAD/A_GRC18_BD_CFD_HALF_CAR_ASSEMBLY_Rev1.x_t
2018_Aero/CFD CAD/Frontal Area Sketches.SLDPRT
2018_Aero/CFD CAD/Nosecone - Surface Only.SLDPRT
2018_Aero/CFD CAD/P_GRC18_BD_CFD_BODY_Rev1.SLDPRT
2018_Aero/CFD CAD/P_GRC18_BD_CFD_BODY_Rev1.x_t
2018_Aero/CFD CAD/P_GRC18_BD_CFD_HALFBODY_Rev1.SLDPRT
2018_Aero/CFD CAD/P_GRC18_BD_CFD_HALFBODY_Rev1.x_t
2018_Aero/CFD CAD/P_GRC18_BD_CFD_HALFNOSECONE_Rev1.x_t
2018_Aero/CFD CAD/P_GRC18_BD_CFD_NOSECONE_Rev1.SLDPRT
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

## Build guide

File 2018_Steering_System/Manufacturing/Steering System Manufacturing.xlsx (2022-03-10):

Part(s) | Steps | Done By | Part(s) | Steps | Done By
Rack Gear | Lathe - Turn to diameter, length, bore out ends | 2019-02-01 | Lower Column 1 | Lathe - Turn to length, diameters | 2020-02-01
 | Tap ends | 2020-02-01 | Lower Column 2 | Lathe - Turn to length, diameter | 2020-02-01
 | Mill - Cuts in middle | 2020-02-01 | Middle Column 1 | Lathe - Turn to length, diameters | 2020-02-01
 | Truegear - Teeth hobbed out | 2001-03-01 | Middle Column 2 | Lathe - Turn to length, diameter | 2020-02-01
Housing Tubes | Lathe - Turn to diameter, length | 2022-02-01 | Upper Column 1 | Lathe - Turn to length, diameters | 2022-02-01
 | Press in bushing | 2022-02-01 | Upper Column 2 | Lathe - Turn to length, diameter | 2022-02-01
 | Mill - Cutouts on end | 2022-02-01 | U-Joints | Shorten | 2024-02-01
Bronze Bushings | Lathe - Turn to length | 2022-02-01 | Pillow Blocks | Mill - Mill to size, drill holes, tap | 2024-02-01
Clevis Joints | Lathe - Turn to length, diameters, bore through | 2022-02-01 |  | Sand the contours | 2024-02-01
 | Mill - Mill out center, make rod end holes | 2022-02-01 |  | Press in bearings | 2024-02-01
 | Thread ends with die | 2022-02-01 | Housing | Bend sheet metal | 2027-02-01
Pinion Gear | Bore out center | 2024-02-01 |  | Drill holes, make cutouts | 2027-02-01
 | Make steering sensor tabs | 2024-02-01 | Bolts | Trim M4, M6 (socket), M6 (hex), M8 | 2018-03-01
Mounts | Write CAM | 2025-02-01 | Full Assembly | Weld together | 2018-03-01
 | Run it | 2026-02-01
 | Drill holes, tap | 2026-02-01
Housing Cover Mold | Write CAM | 2026-02-01
 | Run it | 2026-02-01
Housing Cover | Do carbon fiber | 2028-02-01
Housing | Write CAM | 2028-02-01
 | Run it | 2028-02-01
 | Tap | 2028-02-01
Top Plate | Write CAM | 2028-02-01
 | Run it | 2028-02-01
 | Tap | 2028-02-01
Bottom Plate | Write CAM | 2028-02-01
 | Run it | 2028-02-01
 | Tap | 2028-02-01
Full Assembly | Bond cover, housing tubes, and mounts | 2018-03-01
 | Loctite, grease | 2018-03-01

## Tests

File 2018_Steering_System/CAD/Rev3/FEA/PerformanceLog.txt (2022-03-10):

Mesh Preparation:  0 hr 0 min 0 sec
Standard solid mesh bolt head imprint and hard point processing:  0 hr 0 min 0 sec
Standard solid mesh total preparation including imprint:  0 hr 0 min 1 sec
Standard surface meshing for Solid Mesh:  0 hr 0 min 0 sec
Standard volume meshing for Solid Mesh:  0 hr 0 min 1 sec
Standard surface meshing for Solid Mesh:  0 hr 0 min 0 sec
Standard volume meshing for Solid Mesh:  0 hr 0 min 1 sec
Standard solid mesh arranging data:  0 hr 0 min 0 sec
Standard solid mesh total:  0 hr 0 min 2 sec
Beam mesh:  0 hr 0 min 0 sec
Preparing to transfer data:  0 hr 0 min 2 sec
Processing material properties:  0 hr 0 min 0 sec
Processing element groups:  0 hr 0 min 0 sec
Processing drop test gap nodes:  0 hr 0 min 0 sec
Updating thickness for shell regions:  0 hr 0 min 0 sec
Processing rconst for elements:  0 hr 0 min 0 sec
Processing egroups:  0 hr 0 min 0 sec
Transferring loads and boundary conditions:  0 hr 0 min 0 sec
Generating body pairs to check contact:  0 hr 0 min 0 sec
Generating contacts:  0 hr 0 min 0 sec
Number of Contacts: 0
Transfer SL1 data:  0 hr 0 min 0 sec
Generate more accurate contact data:  0 hr 0 min 0 sec
Number of contact data: 0
Transfer beam/joint contact data:  0 hr 0 min 0 sec
Transferring other special loads:  0 hr 0 min 0 sec
Transferring bearing loads:  0 hr 0 min 0 sec
Transferring mass elements:  0 hr 0 min 0 sec
Transferring point loads:  0 hr 0 min 0 sec
Transferring distributed beam loads:  0 hr 0 min 0 sec
Transferring rigid bodies:  0 hr 0 min 0 sec
Transferring component no penetration:  0 hr 0 min 0 sec
Writing Data:  0 hr 0 min 0 sec
Transferring analysis options:  0 hr 0 min 0 sec
Total midsurf mapping:  0 hr 0 min 0 sec

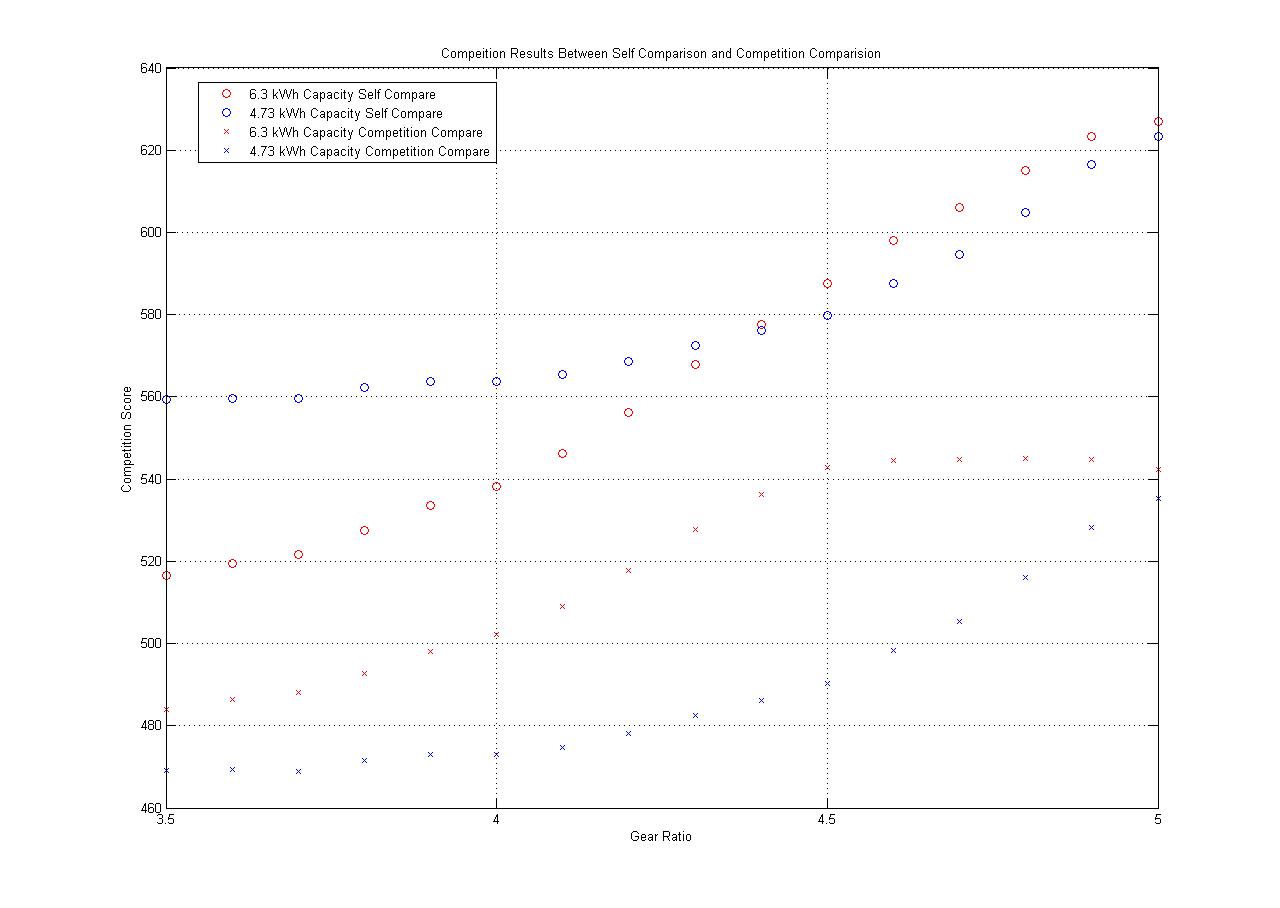
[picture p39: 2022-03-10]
2019_Suspension_Design/Simulation/LapSimFE-master/Plots/FSG2013TrackResults.jpg

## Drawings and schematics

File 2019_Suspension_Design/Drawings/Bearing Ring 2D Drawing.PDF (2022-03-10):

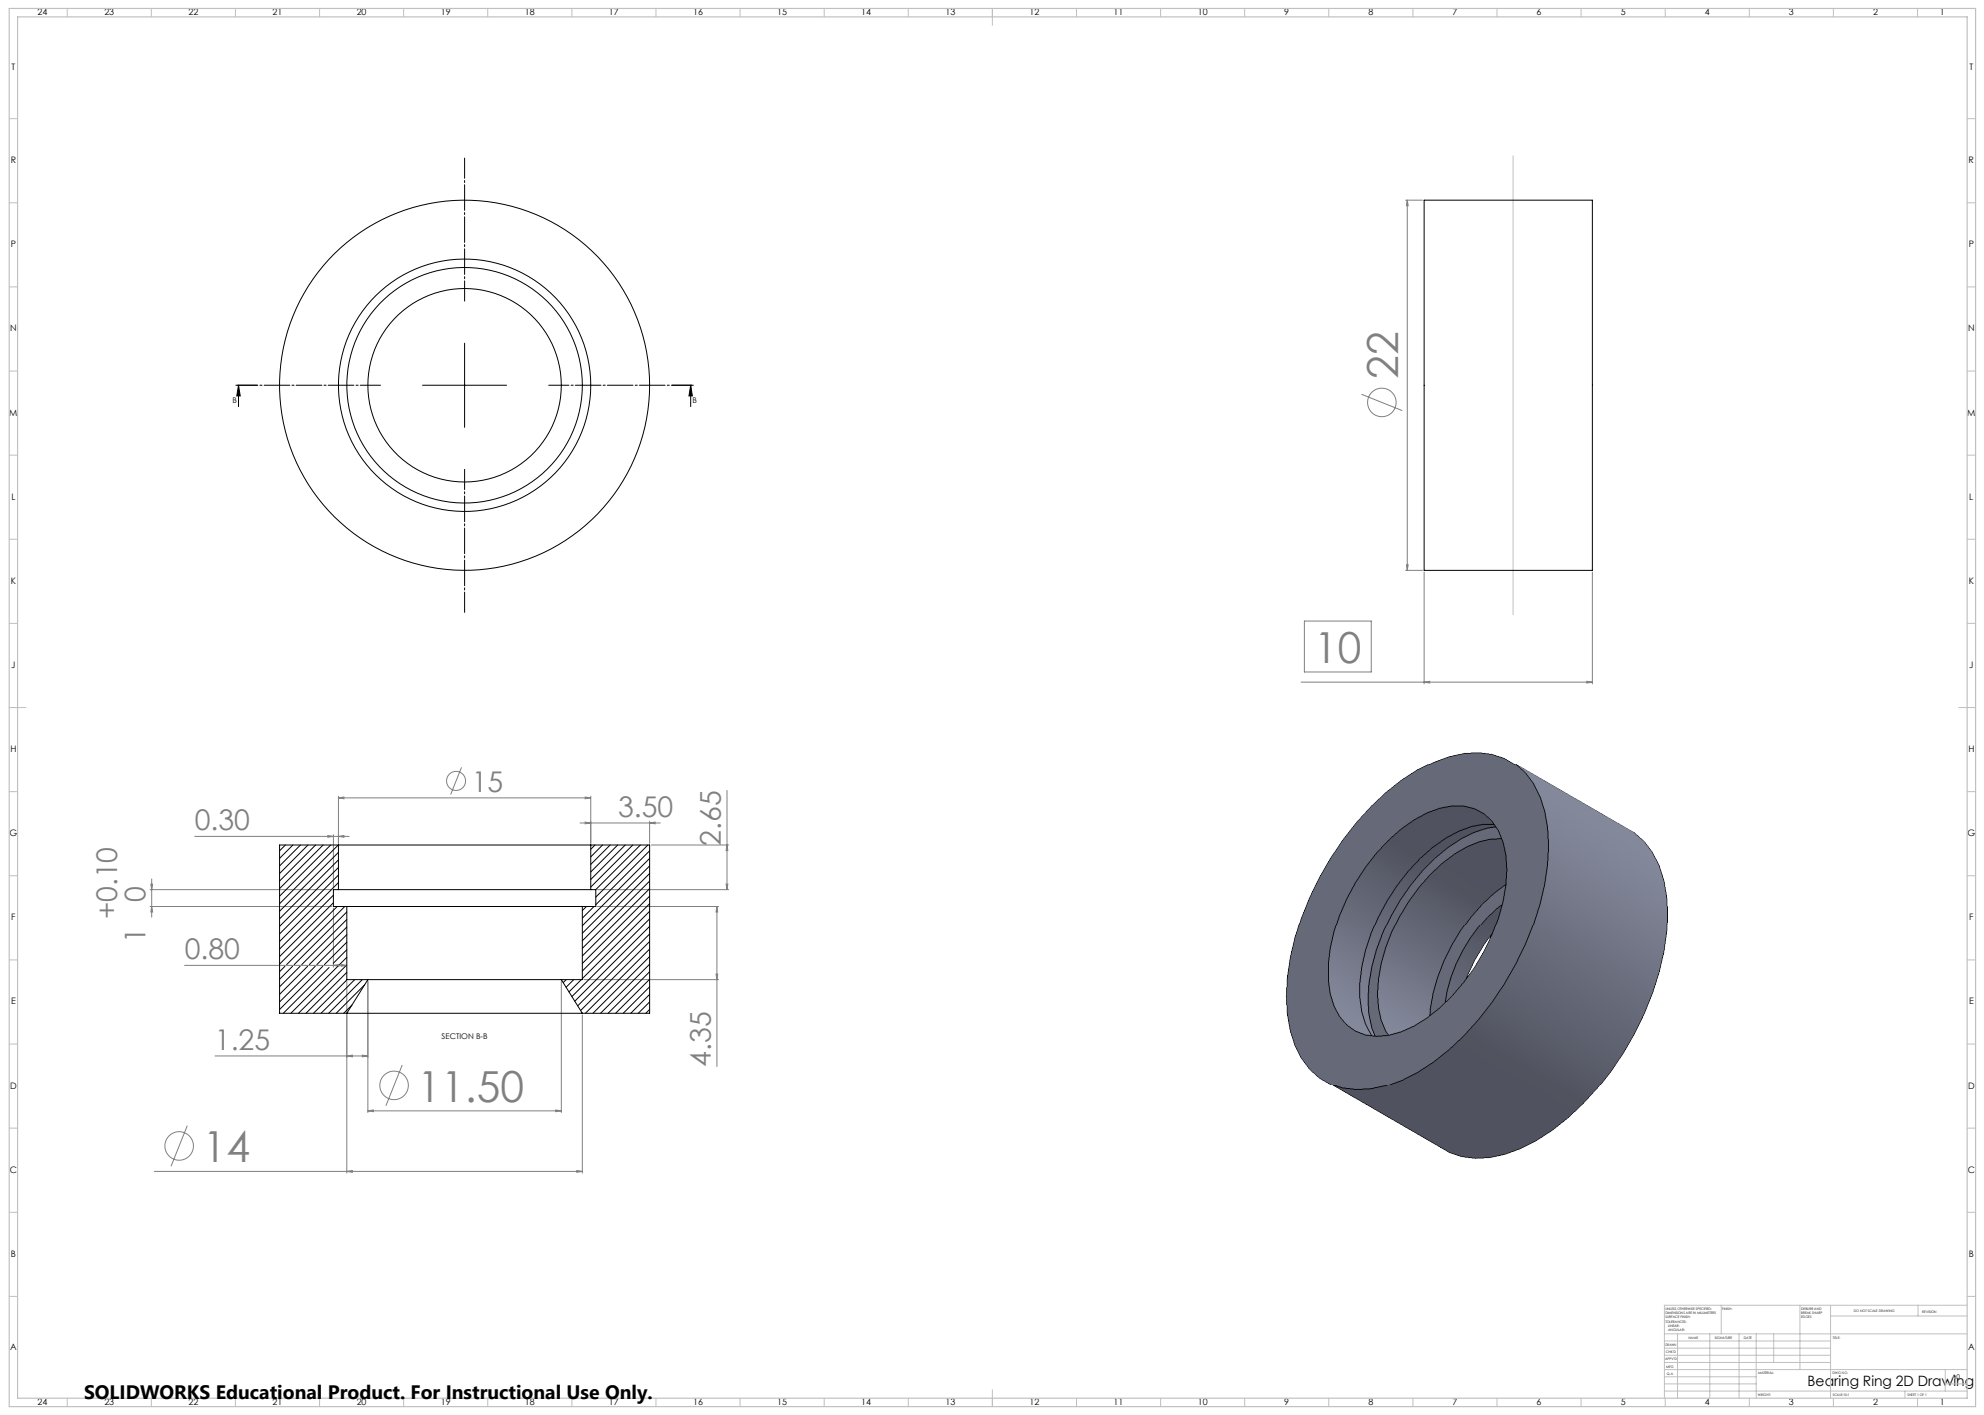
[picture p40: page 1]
SECTION B-B; FINISH:; DEBURR AND; BREAK SHARP; DO NOT SCALE DRAWING; REVISION; SCALE:10:1; SHEET 1 OF 1

UNLESS OTHERWISE SPECIFIED:
DIMENSIONS ARE IN MILLIMETERS
SURFACE FINISH:
TOLERANCES:
LINEAR:
ANGULAR:

NAME | SIGNATURE | DATE | | | | TITLE:

Bearing Ring 2D Drawing SOLIDWORKS Educational Product. For Instructional Use Only.

DRAWN
CHK'D
APPV'D
MFG
Q.A | | | | MATERIAL: | DWG NO. | A0

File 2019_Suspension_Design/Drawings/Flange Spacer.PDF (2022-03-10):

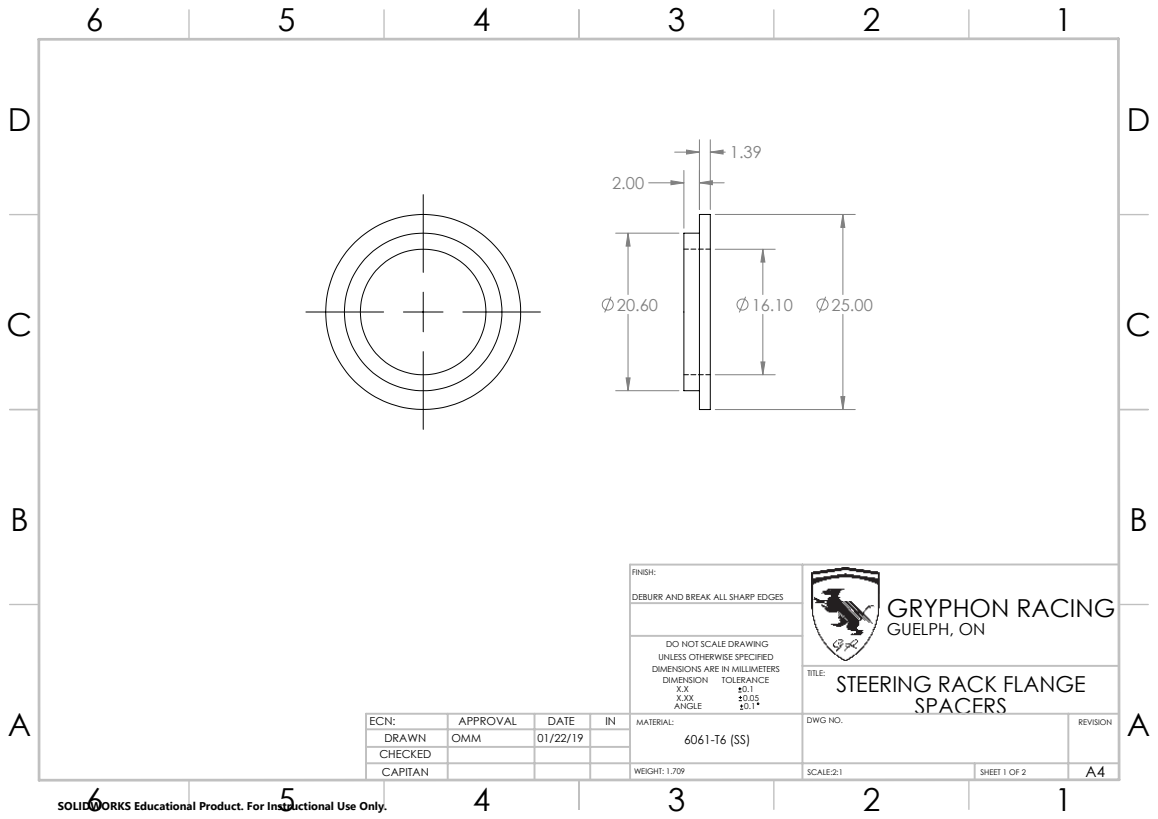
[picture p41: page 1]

DEBURR AND BREAK ALL SHARP EDGES

GRYPHON RACING
GUELPH, ON
STEERING RACK FLANGE
SPACERS

DO NOT SCALE DRAWING
UNLESS OTHERWISE SPECIFIED
DIMENSIONS ARE IN MILLIMETERS

SOLIDWORKS Educational Product. For Instructional Use Only.

ECN: | APPROVAL | DATE | IN | MATERIAL: 6061-T6 (SS) | DWG NO. | REVISION
DRAWN | OMM | 01/22/19
CHECKED
CAPITAN | | | | WEIGHT: 1.709 | SCALE:2:1 | SHEET 1 OF 2 | A4

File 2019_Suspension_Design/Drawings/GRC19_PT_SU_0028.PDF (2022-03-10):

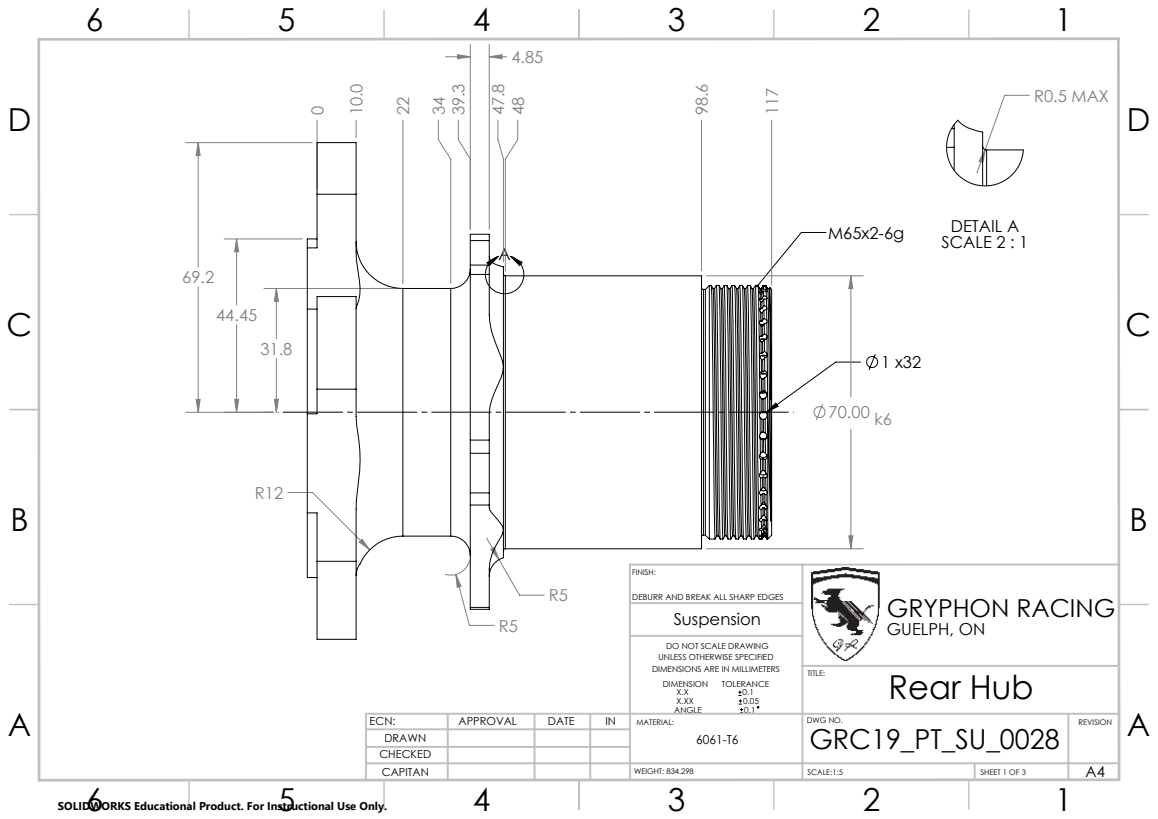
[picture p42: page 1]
R0.5 MAX; DETAIL A SCALE 2 : 1; Rear Hub; GRYPHON RACING GUELPH, ON

DEBURR AND BREAK ALL SHARP EDGES

DO NOT SCALE DRAWING
UNLESS OTHERWISE SPECIFIED
DIMENSIONS ARE IN MILLIMETERS

ECN: | APPROVAL | DATE | IN | MATERIAL: 6061-T6 | DWG NO. GRC19_PT_SU_0028 | REVISION
DRAWN
CHECKED
CAPITAN | | | | WEIGHT: 834.298 | SCALE:1:5 | SHEET 1 OF 3 | A4

SOLIDWORKS Educational Product. For Instructional Use Only.

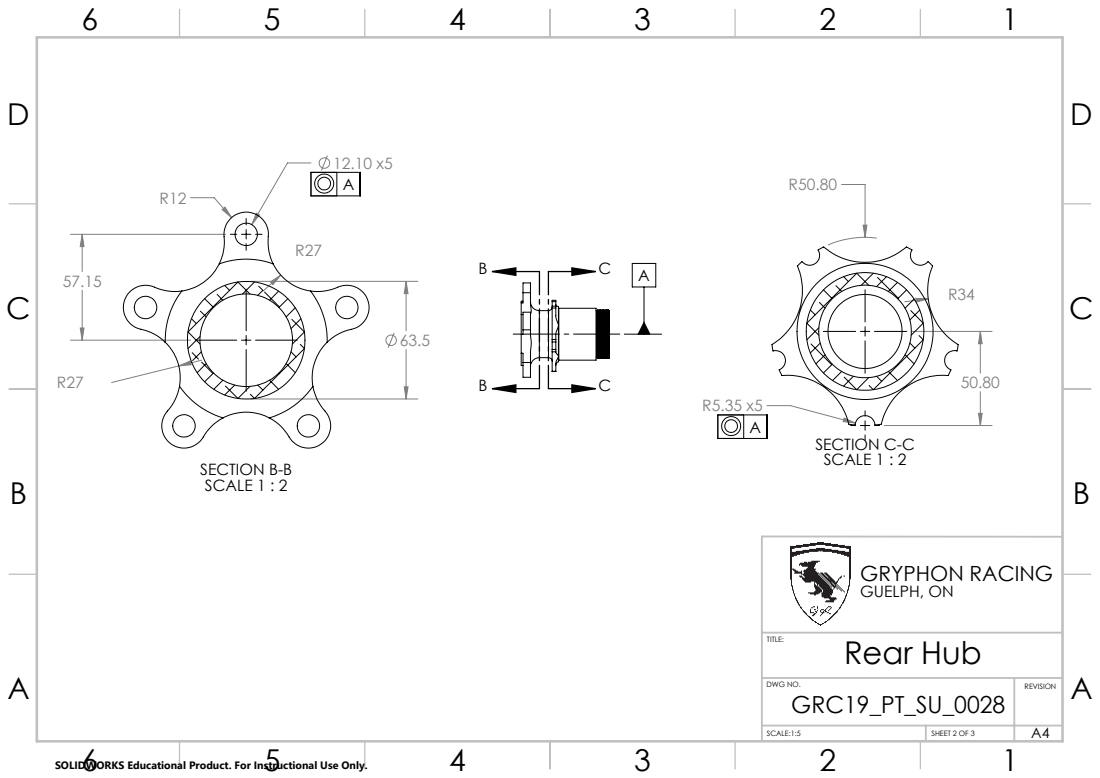
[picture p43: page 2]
SECTION B-B SCALE 1 : 2; SECTION C-C SCALE 1 : 2; Rear Hub; GRYPHON RACING GUELPH, ON

DWG NO. GRC19_PT_SU_0028 | REVISION

SCALE:1:5 | SHEET 2 OF 3 | A4

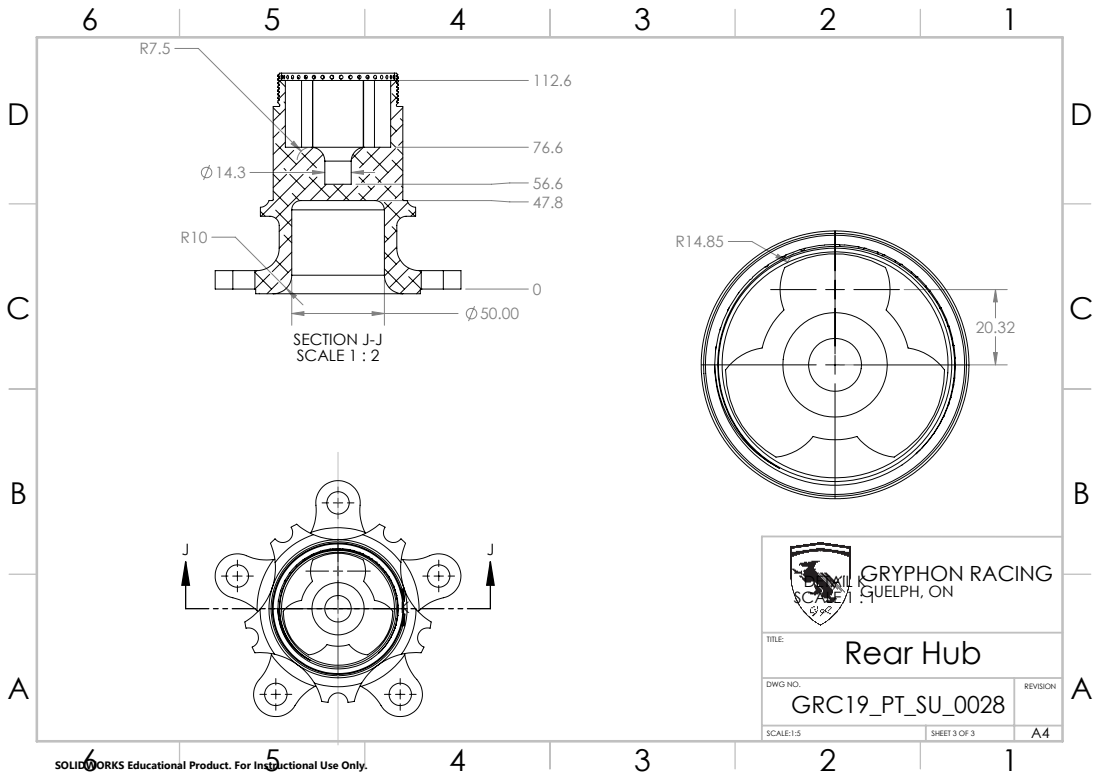
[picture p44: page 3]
SECTION J-J SCALE 1 : 2; DETAIL K SCALE 1 : 1 Rear Hub; GRYPHON RACING GUELPH, ON

DWG NO. GRC19_PT_SU_0028 | REVISION

SCALE:1:5 | SHEET 3 OF 3 | A4

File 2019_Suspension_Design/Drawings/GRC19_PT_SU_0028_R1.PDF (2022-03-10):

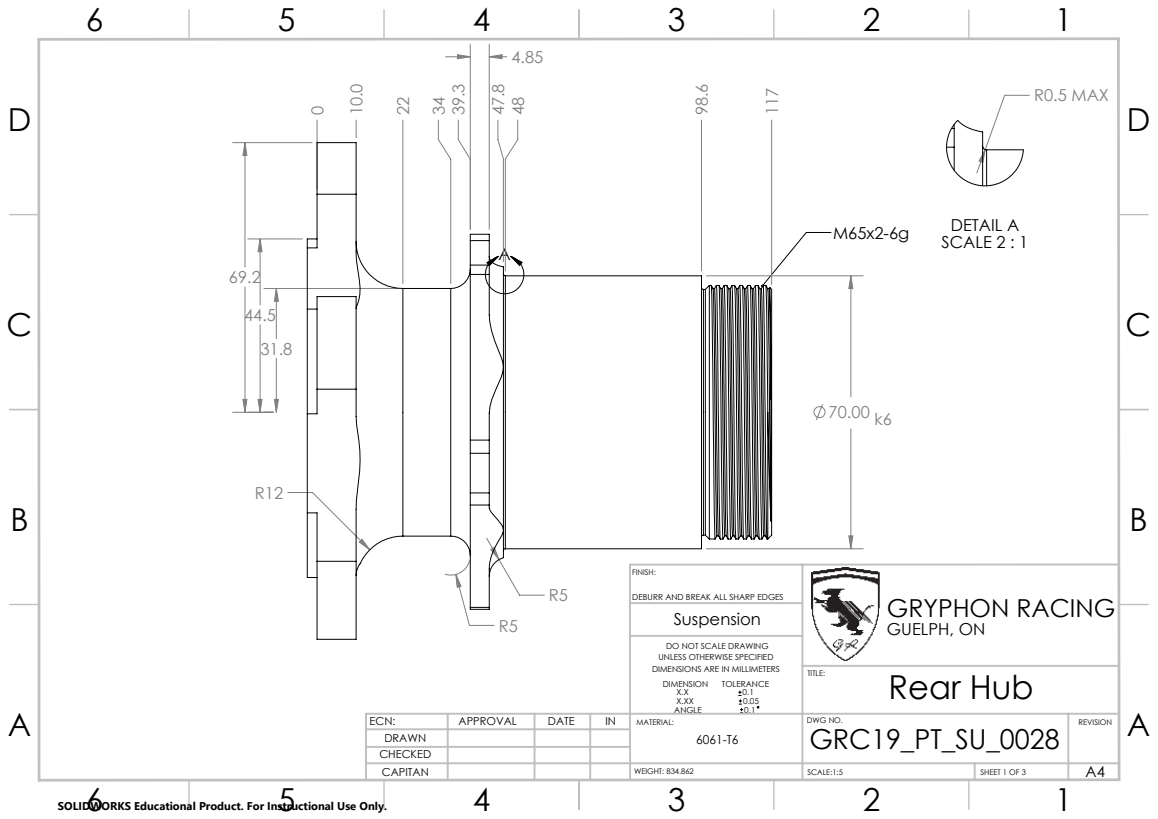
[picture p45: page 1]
R0.5 MAX; DETAIL A SCALE 2 : 1; Rear Hub; GRYPHON RACING GUELPH, ON

DEBURR AND BREAK ALL SHARP EDGES

DO NOT SCALE DRAWING
UNLESS OTHERWISE SPECIFIED
DIMENSIONS ARE IN MILLIMETERS

ECN: | APPROVAL | DATE | IN | MATERIAL: 6061-T6 | DWG NO. GRC19_PT_SU_0028 | REVISION
DRAWN
CHECKED
CAPITAN | | | | WEIGHT: 834.862 | SCALE:1:5 | SHEET 1 OF 3 | A4

SOLIDWORKS Educational Product. For Instructional Use Only.

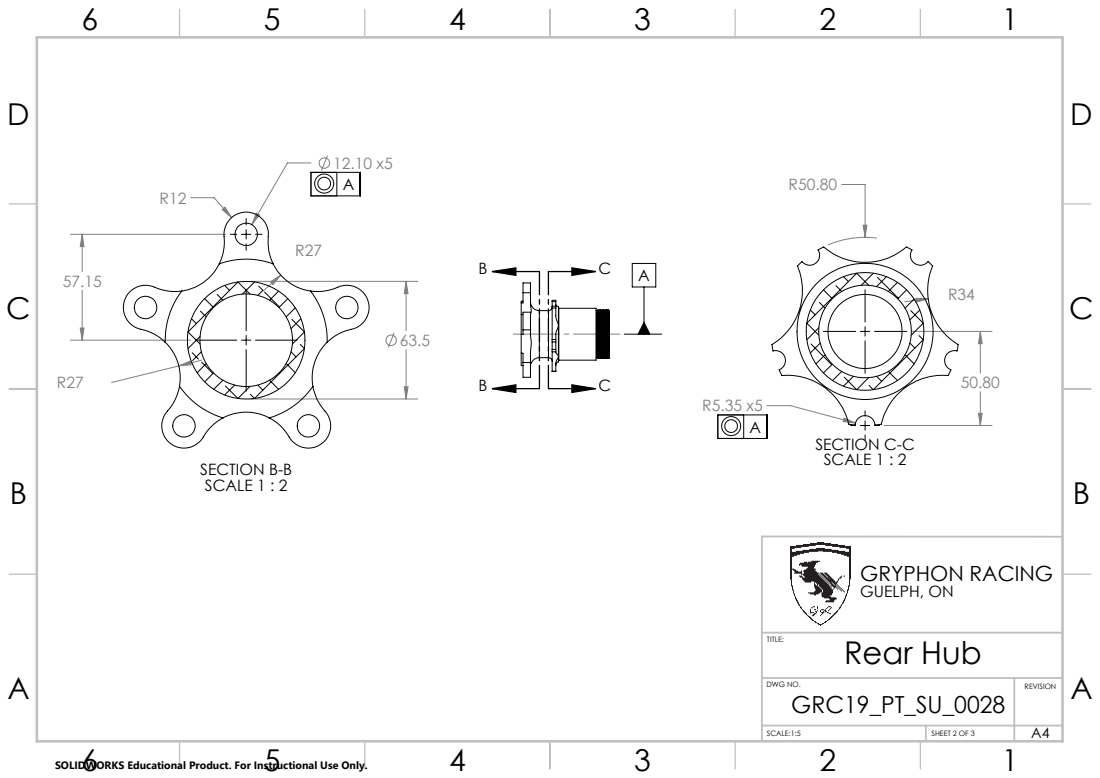
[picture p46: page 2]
SECTION B-B SCALE 1 : 2; SECTION C-C SCALE 1 : 2; Rear Hub; GRYPHON RACING GUELPH, ON

DWG NO. GRC19_PT_SU_0028 | REVISION

SCALE:1:5 | SHEET 2 OF 3 | A4

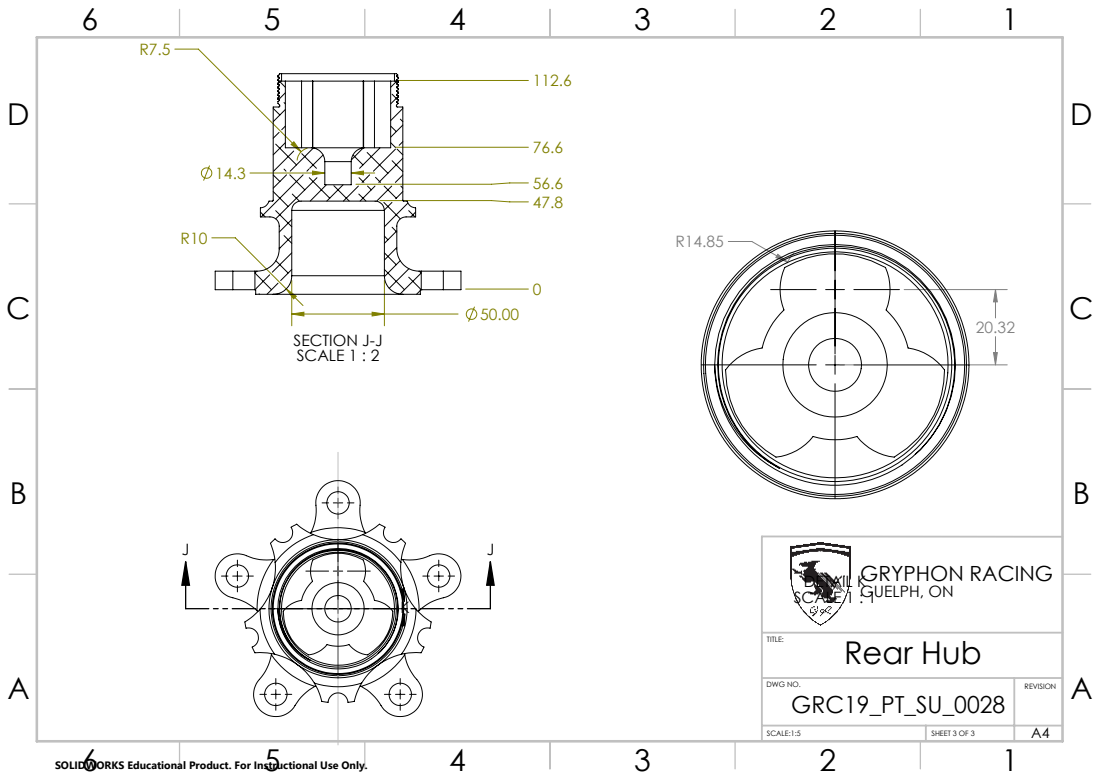
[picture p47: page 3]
SECTION J-J SCALE 1 : 2; DETAIL K SCALE 1 : 1 Rear Hub; GRYPHON RACING GUELPH, ON

DWG NO. GRC19_PT_SU_0028 | REVISION

SCALE:1:5 | SHEET 3 OF 3 | A4

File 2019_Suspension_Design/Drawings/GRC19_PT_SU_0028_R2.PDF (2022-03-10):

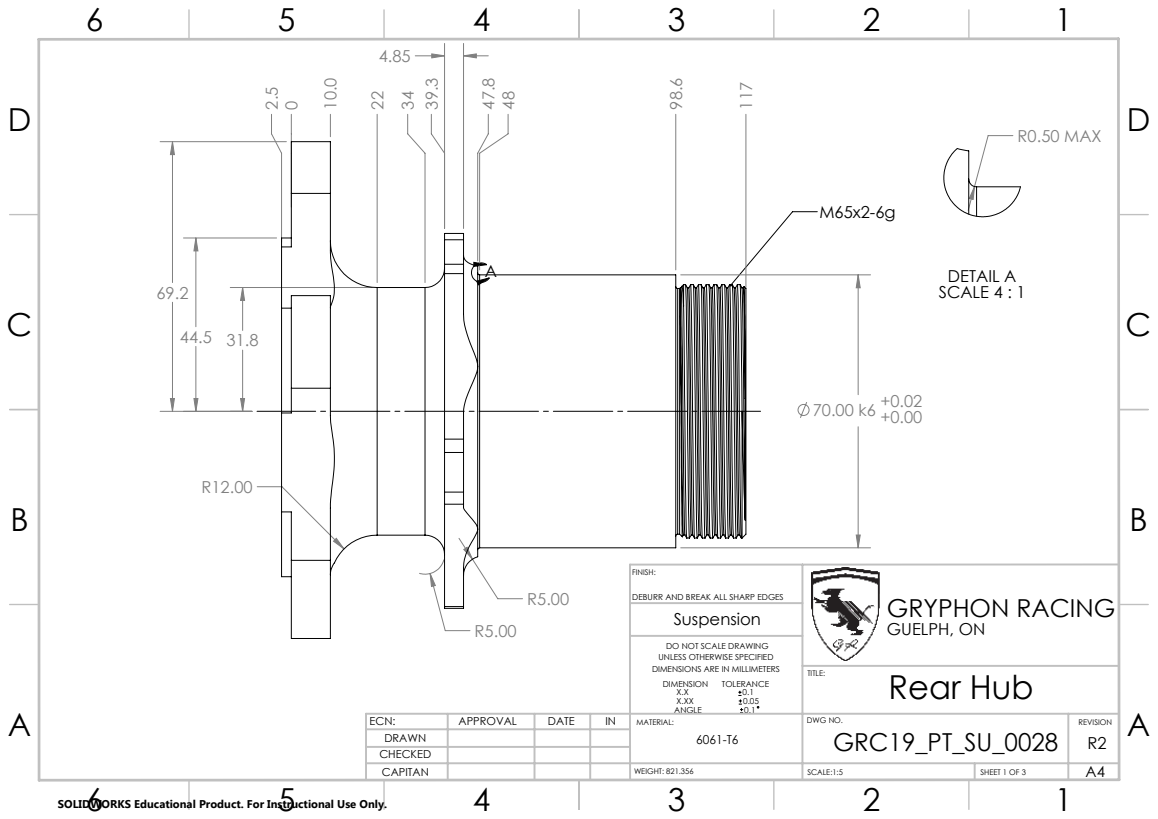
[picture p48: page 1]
R0.50 MAX; DETAIL A SCALE 4 : 1; Rear Hub; GRYPHON RACING GUELPH, ON

DEBURR AND BREAK ALL SHARP EDGES

DO NOT SCALE DRAWING
UNLESS OTHERWISE SPECIFIED
DIMENSIONS ARE IN MILLIMETERS

ECN: | APPROVAL | DATE | IN | MATERIAL: 6061-T6 | DWG NO. GRC19_PT_SU_0028 | REVISION R2
DRAWN
CHECKED
CAPITAN | | | | WEIGHT: 821.356 | SCALE:1:5 | SHEET 1 OF 3 | A4

SOLIDWORKS Educational Product. For Instructional Use Only.

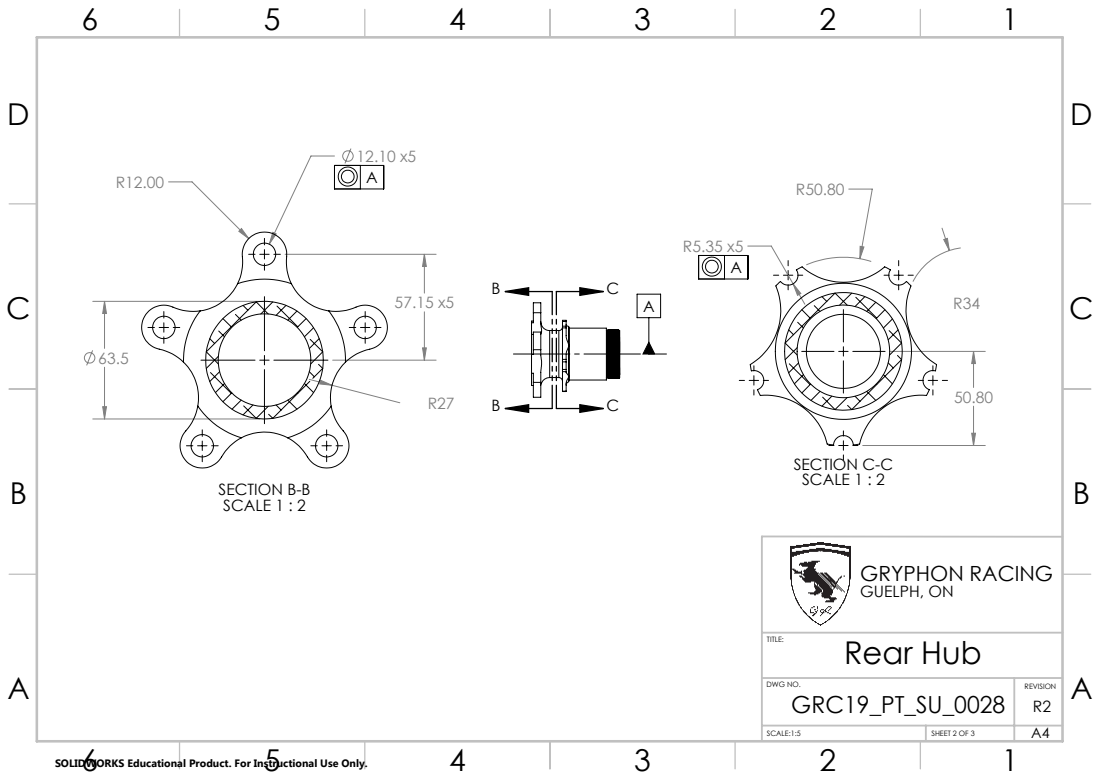
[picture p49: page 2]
SECTION B-B SCALE 1 : 2; SECTION C-C SCALE 1 : 2; Rear Hub; GRYPHON RACING GUELPH, ON

DWG NO. GRC19_PT_SU_0028 | REVISION R2

SCALE:1:5 | SHEET 2 OF 3 | A4

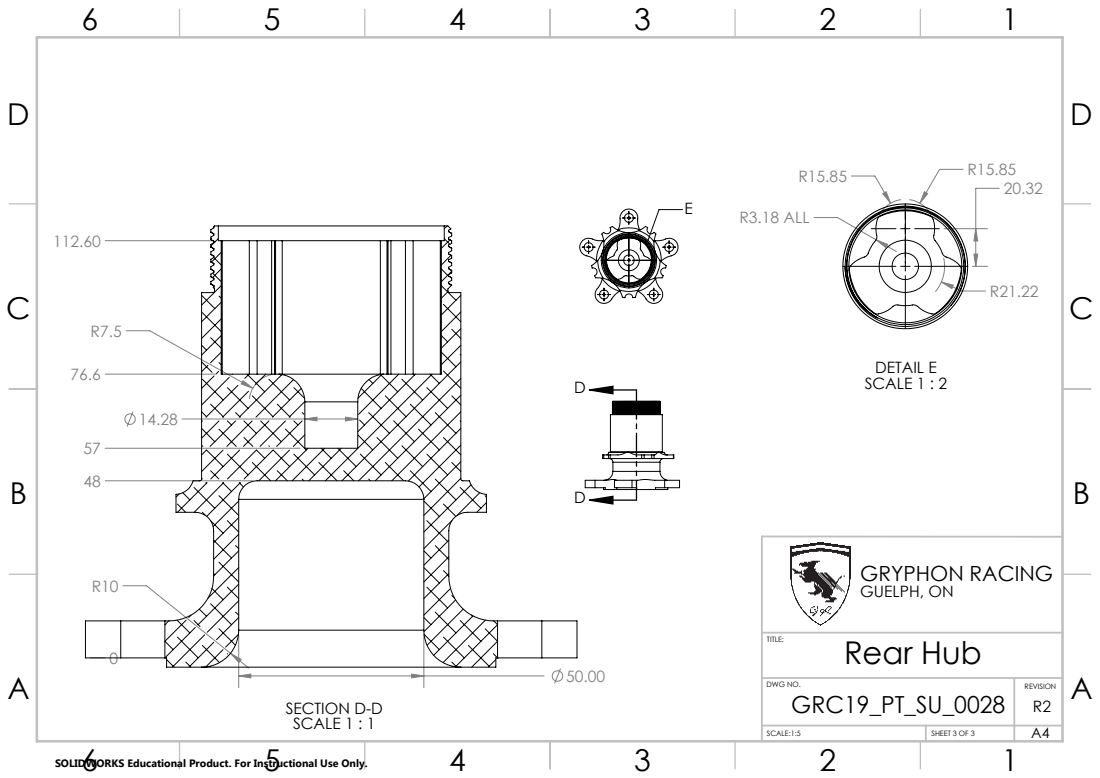
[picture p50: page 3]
SECTION D-D SCALE 1 : 1; R3.18 ALL; DETAIL E SCALE 1 : 2; Rear Hub; GRYPHON RACING GUELPH, ON

DWG NO. GRC19_PT_SU_0028 | REVISION R2

SCALE:1:5 | SHEET 3 OF 3 | A4

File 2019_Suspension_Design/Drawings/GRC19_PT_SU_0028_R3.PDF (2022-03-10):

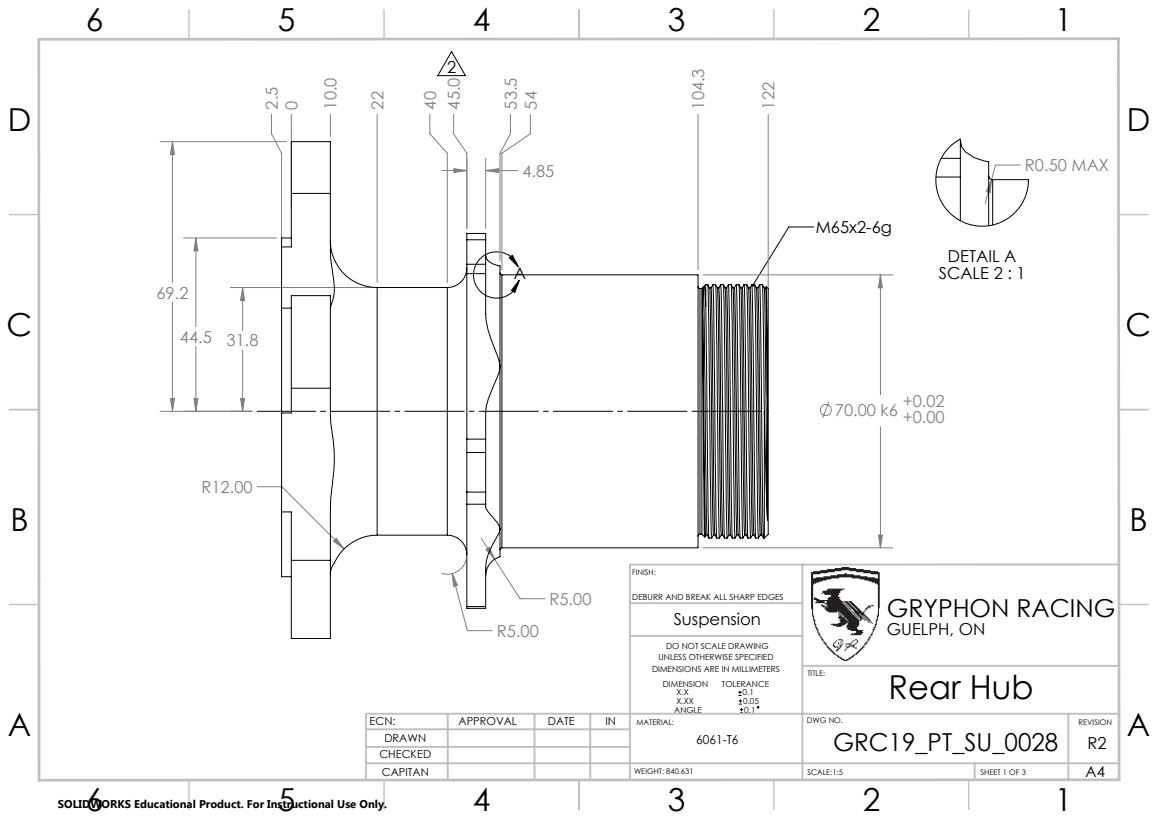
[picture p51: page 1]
R0.50 MAX; DETAIL A SCALE 2 : 1; Rear Hub; GRYPHON RACING GUELPH, ON

DEBURR AND BREAK ALL SHARP EDGES

DO NOT SCALE DRAWING
UNLESS OTHERWISE SPECIFIED
DIMENSIONS ARE IN MILLIMETERS

ECN: | APPROVAL | DATE | IN | MATERIAL: 6061-T6 | DWG NO. GRC19_PT_SU_0028 | REVISION R2
DRAWN
CHECKED
CAPITAN | | | | WEIGHT: 840.631 | SCALE:1:5 | SHEET 1 OF 3 | A4

SOLIDWORKS Educational Product. For Instructional Use Only.

SECTION B-B SCALE 1 : 2; SECTION C-C SCALE 1 : 2; Rear Hub; GRYPHON RACING GUELPH, ON

DWG NO. GRC19_PT_SU_0028 | REVISION R2

SCALE:1:5 | SHEET 2 OF 3 | A4

SECTION D-D SCALE 1 : 1; R3.18 ALL; DETAIL E SCALE 1 : 2; Rear Hub; GRYPHON RACING GUELPH, ON

DWG NO. GRC19_PT_SU_0028 | REVISION R2

SCALE:1:5 | SHEET 3 OF 3 | A4

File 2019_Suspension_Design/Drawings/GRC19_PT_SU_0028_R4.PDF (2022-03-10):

R0.50 MAX; DETAIL A SCALE 2 : 1; Rear Hub; GRYPHON RACING GUELPH, ON

DEBURR AND BREAK ALL SHARP EDGES

DO NOT SCALE DRAWING
UNLESS OTHERWISE SPECIFIED
DIMENSIONS ARE IN MILLIMETERS

ECN: | APPROVAL | DATE | IN | MATERIAL: 6061-T6 | DWG NO. GRC19_PT_SU_0028 | REVISION R2
DRAWN
CHECKED
CAPITAN | | | | WEIGHT: 840.631 | SCALE:1:5 | SHEET 1 OF 3 | A4

SOLIDWORKS Educational Product. For Instructional Use Only.

SECTION B-B SCALE 1 : 2; SECTION C-C SCALE 1 : 2; Rear Hub; GRYPHON RACING GUELPH, ON

DWG NO. GRC19_PT_SU_0028 | REVISION R2

SCALE:1:5 | SHEET 2 OF 3 | A4

SECTION D-D SCALE 1 : 1; R3.18 ALL; DETAIL E SCALE 1 : 2; Rear Hub; GRYPHON RACING GUELPH, ON

DWG NO. GRC19_PT_SU_0028 | REVISION R2

SCALE:1:5 | SHEET 3 OF 3 | A4

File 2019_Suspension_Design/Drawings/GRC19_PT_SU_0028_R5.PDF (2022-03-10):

R0.50 MAX; DETAIL A SCALE 2 : 1; Rear Hub; GRYPHON RACING GUELPH, ON

DEBURR AND BREAK ALL SHARP EDGES

DO NOT SCALE DRAWING
UNLESS OTHERWISE SPECIFIED
DIMENSIONS ARE IN MILLIMETERS

ECN: | APPROVAL | DATE | IN | MATERIAL: 6061-T6 | DWG NO. GRC19_PT_SU_0028 | REVISION R2
DRAWN
CHECKED
CAPITAN | | | | WEIGHT: 840.308 | SCALE:1:5 | SHEET 1 OF 3 | A4

SOLIDWORKS Educational Product. For Instructional Use Only.

SECTION B-B SCALE 1 : 2; SECTION C-C SCALE 1 : 2; Rear Hub; GRYPHON RACING GUELPH, ON

DWG NO. GRC19_PT_SU_0028 | REVISION R2

SCALE:1:5 | SHEET 2 OF 3 | A4

SECTION D-D SCALE 1 : 1; R3.18 ALL; DETAIL E SCALE 1 : 2; Rear Hub; GRYPHON RACING GUELPH, ON

DWG NO. GRC19_PT_SU_0028 | REVISION R2

SCALE:1:5 | SHEET 3 OF 3 | A4

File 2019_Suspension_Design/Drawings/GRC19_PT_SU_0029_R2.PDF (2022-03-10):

SECTION A-A

DEBURR AND BREAK ALL SHARP EDGES

GRYPHON RACING
GUELPH, ON
Rear Hub Nut

DO NOT SCALE DRAWING
UNLESS OTHERWISE SPECIFIED
DIMENSIONS ARE IN MILLIMETERS

SOLIDWORKS Educational Product. For Instructional Use Only.

ECN: | APPROVAL | DATE | IN | MATERIAL: 6061-T6 | DWG NO. GRC19_PT_SU_0029 | REVISION 2
DRAWN
CHECKED
CAPITAN | | | | WEIGHT: 61.215 | SCALE:1:2 | SHEET 1 OF 2 | A4

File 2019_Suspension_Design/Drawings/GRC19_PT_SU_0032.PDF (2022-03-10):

TRIPOD SLEEVE; GRYPHON RACING GUELPH, ON

DEBURR AND BREAK ALL SHARP EDGES

DO NOT SCALE DRAWING
UNLESS OTHERWISE SPECIFIED
DIMENSIONS ARE IN MILLIMETERS

SOLIDWORKS Educational Product. For Instructional Use Only.

ECN: | APPROVAL | DATE | IN | MATERIAL: AISI 4340 Steel, normalized | DWG NO. GRC19_PT_SU_0032 | REVISION 2
DRAWN
CHECKED
CAPITAN | | | | WEIGHT: 120.064 | SCALE:1:1 | SHEET 1 OF 1 | A4

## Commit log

2022-03-10 add FSAE files - documents, code, small assemblies
    [13-16 Rack Gear.SLDPRT, 13T-17.4 NARRco Rack V2.SLDPRT, 2018 CFD Body.SLDPRT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]
2022-03-10 un-nest folder
    [2018 CFD Body.SLDPRT, A_GRC18_BD_CFD_FULL_CAR_ASSEMBLY_Rev1.SLDASM, A_GRC18_BD_CFD_HALF_CAR_ASSEMBLY_Rev1.SLDASM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]
2022-03-10 additional files
    [Book1.xlsx, Steering Calculator.xlsx]
